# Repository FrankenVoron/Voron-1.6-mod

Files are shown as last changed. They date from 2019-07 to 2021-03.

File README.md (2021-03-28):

This modification has been transformed to the official Voron V1.8! https://github.com/VoronDesign/Voron-1/tree/Voron1.8

The files here are no longer maintained but will be kept for reference.

# Voron-1.6-mod (Depreciated)

It's the Voron V1.6, but better! Now with linear rails for XY and a fully enclosable design.

This github page is being updated and developed. Please note that all of these STLs are derived from the Voron Design V1.6 and V2.1 printers--any mods present in this folder are small changes to the existing Voron Design STLs to support changing the linear rods of V1.6 to linear MGN9H rails similar to how V2.1's gantry is.

This mod is fully unsupported by the Voron Design team, support and discussion will be in a separate Discord group, link to be populated in the future.

Default size is 300x300x340mm, reducing it down to 250mm saves only about $25. 340mm is due to lack of availability of 360mm linear steppers.

Total BOM cost is around $750-800, which sits it between the Hypercube ($550), BLV MGN Cube ($1000) and the Railcore II 300ZL ($1300). 

Advantages over the HEVO:
    
    -Cast aluminum bed (vs. PCB bed) -> much flatter, consistent bed surface
    -Linear rails for XY (vs. linear rods) -> less sag
    -AC heated bed (lower current to the bed, less load on the 24V power supply, quieter)
    -SKR 1.3 board with silent TMC2209 drivers vs. RAMPS board and loud A4988 drivers
    -Integrated Octoprint remote web control through Raspberry Pi
    -True 32 bit board with Klipper control
    -Mobius 3 extruder with Bondtech gears vs. Titan extruder (higher torque, grabs filament from both sides)
    -Enclosed build volume

Advantages over the Railcore:
    
    -Significantly cheaper
    -Easily enclosable
    -No risk of catching hands or tools on CoreXY belts

[V1.6 Mod BOM Link (In Process, NOT FINAL)](https://docs.google.com/spreadsheets/d/1ig14b1j8-F_122QWTeGj5dSmB8Jl30DImUAANSiHRPc/edit?usp=sharing)

[V1.6 Mod Fusion 360 Assembly (300^3)](https://a360.co/2MlttV1) <- will be updated to 300x300x340mm

V1.6 Mod

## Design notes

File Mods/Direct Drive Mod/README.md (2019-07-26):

# FT-V

Beta mod to add a BMG direct drive extruder on to the top of the carriage. Note--the VORON cable cover doors will not fit with this mod, and it may be difficult to find a place for the wires in your hotend. 

This is largely untested at the moment. Use at your own risk.

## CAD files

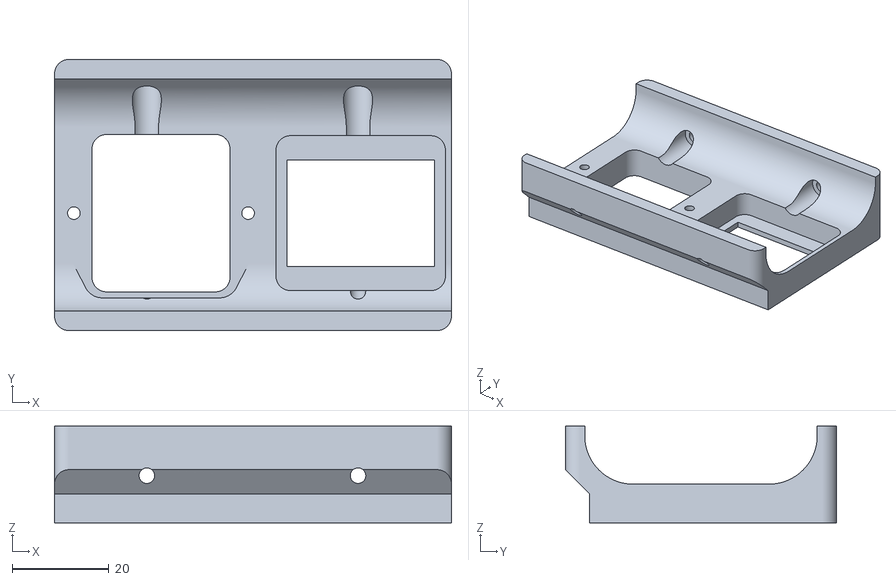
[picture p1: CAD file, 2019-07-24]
STLs/Bottom Skirts (Stock V1.6)/mains_plug_panel_filter_inlet+separate_breaker.STL
82.0 x 56.0 x 20.0

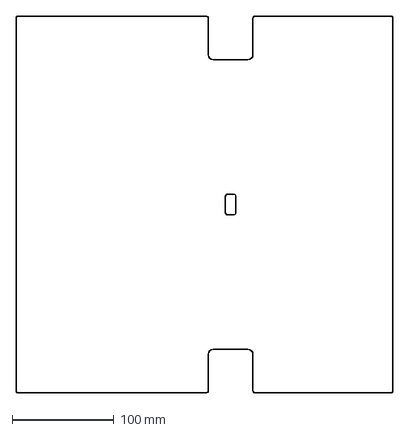
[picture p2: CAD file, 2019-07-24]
DXFs/Deck Panel - Stock^3.DXF
370.0 x 370.0 mm

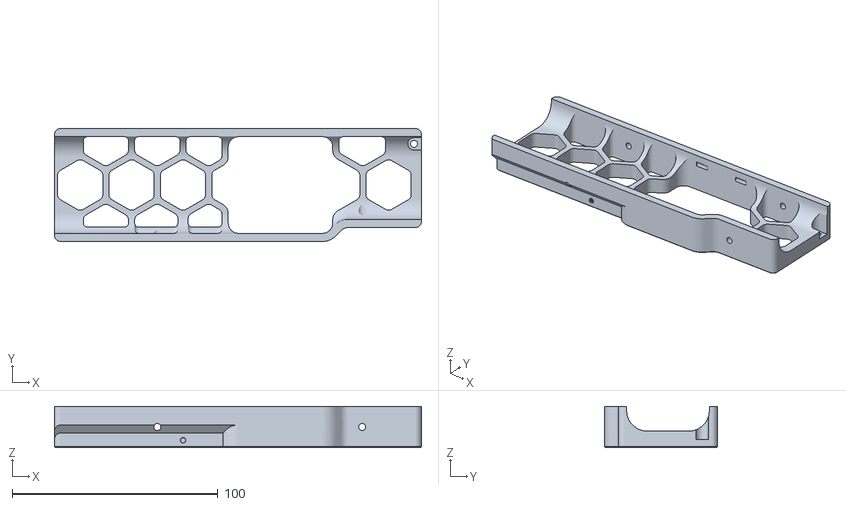
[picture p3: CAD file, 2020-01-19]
Mods/Bottom Skirts 300 Spec/front_rear_skirt_b_x2.stl
178.5 x 55.0 x 20.0

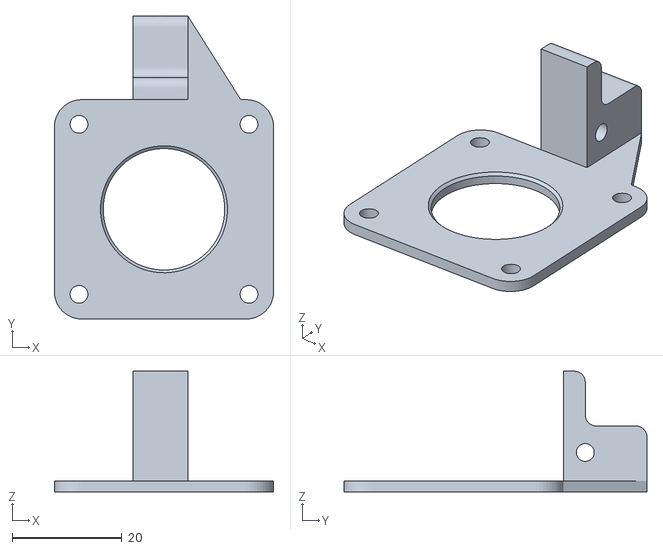
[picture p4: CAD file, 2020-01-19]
Mods/Direct Drive Mod/Direct_Drive_BMG_Mount.stl
40.0 x 55.3 x 22.0

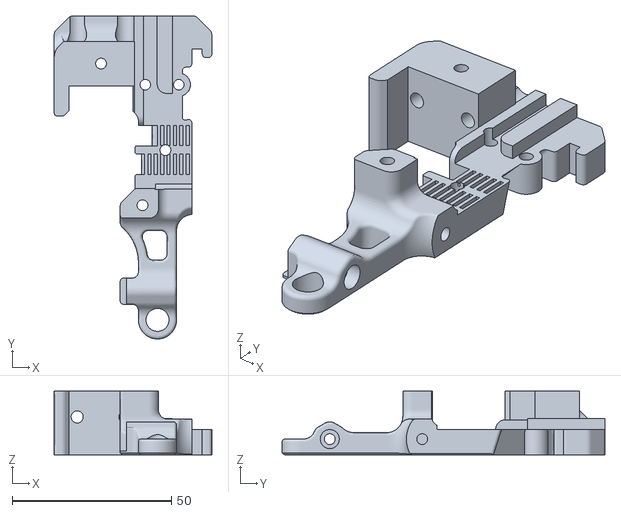
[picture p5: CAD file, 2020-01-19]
Mods/Omron X Carriage/x_carriage_frame_left_omron.stl
49.5 x 101.4 x 20.0

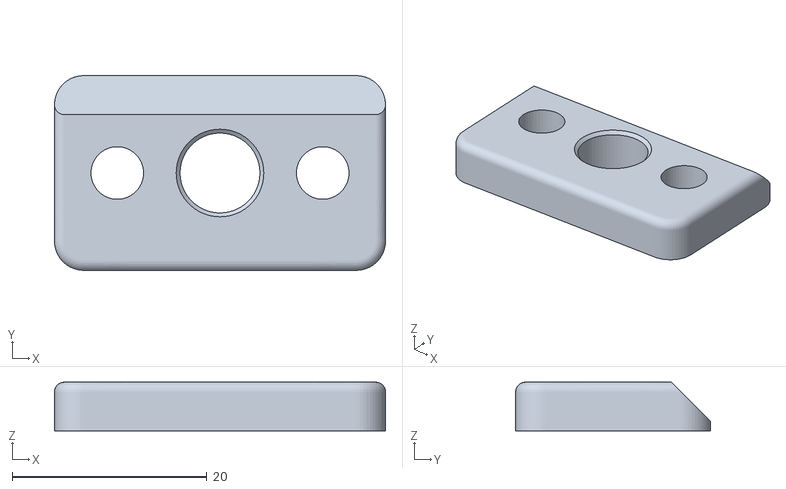
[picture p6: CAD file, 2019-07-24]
STLs/Bed (Stock V1.6)/z_shaft_retainer_x8.stl
34.0 x 20.0 x 5.00

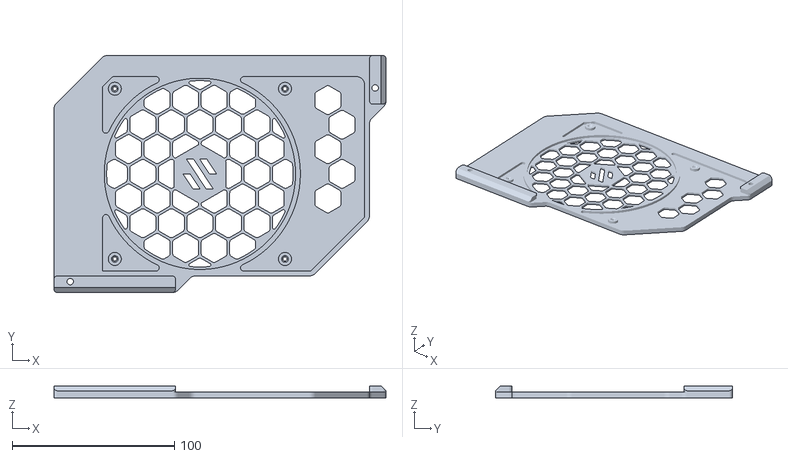
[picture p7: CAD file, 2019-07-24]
STLs/Bottom Skirts (Stock V1.6)/fan_mount.stl
204.8 x 146.2 x 7.70

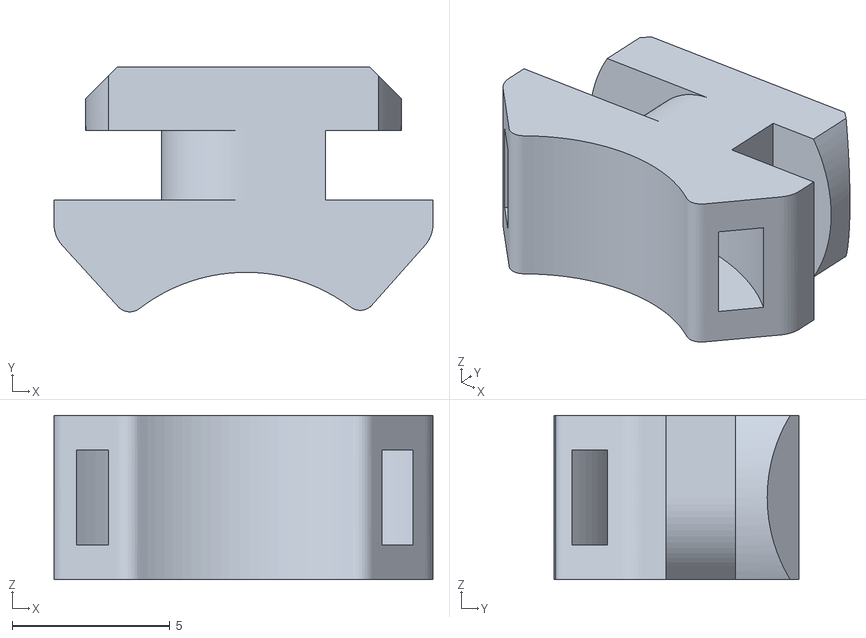
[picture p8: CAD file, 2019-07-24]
STLs/Cable Management (Stock V1.6)/wire_harness_anchor_x5.stl
12.0 x 7.75 x 5.20

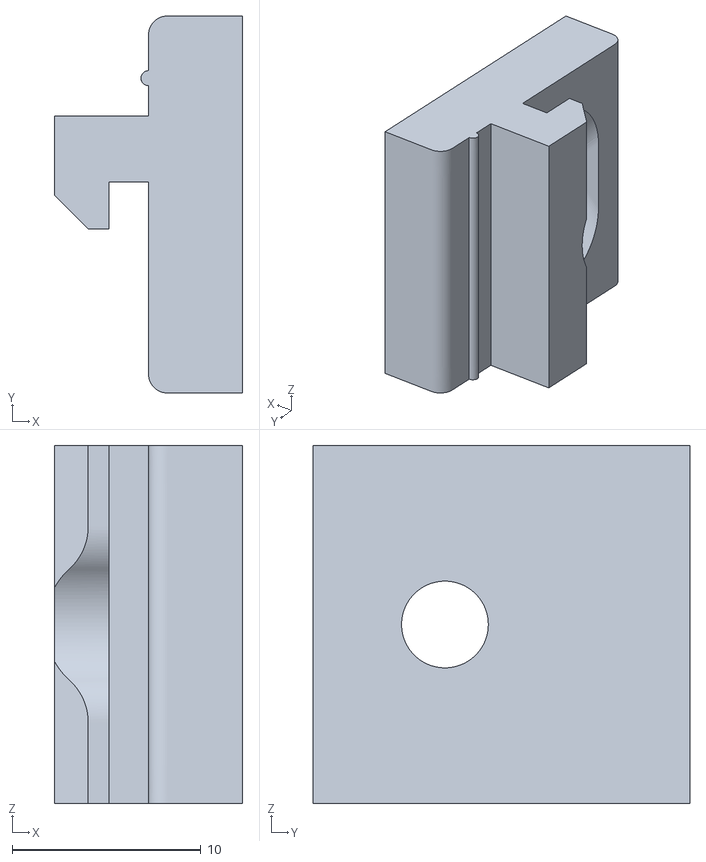
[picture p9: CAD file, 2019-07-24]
STLs/Electronics Brackets (Stock V1.6)/psu_mount_clip_x2.stl
10.0 x 20.0 x 19.0

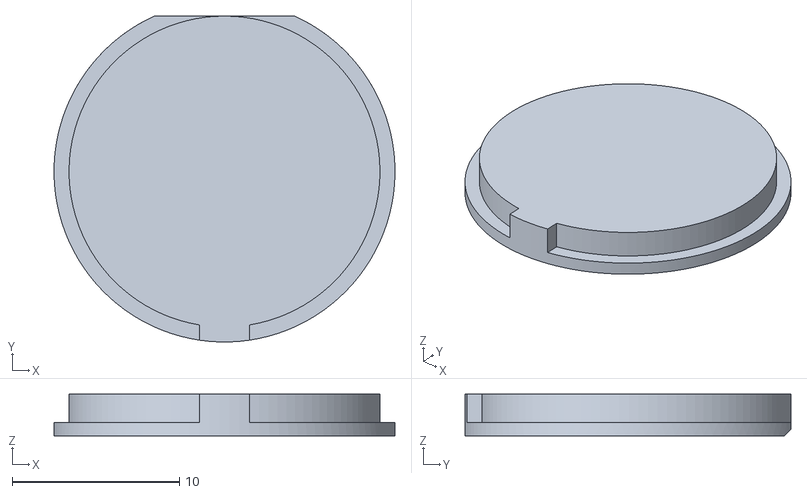
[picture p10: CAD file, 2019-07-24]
STLs/FSR Z Endstop (Stock V1.6)/fsr_strike_plate.stl
20.4 x 19.5 x 2.50

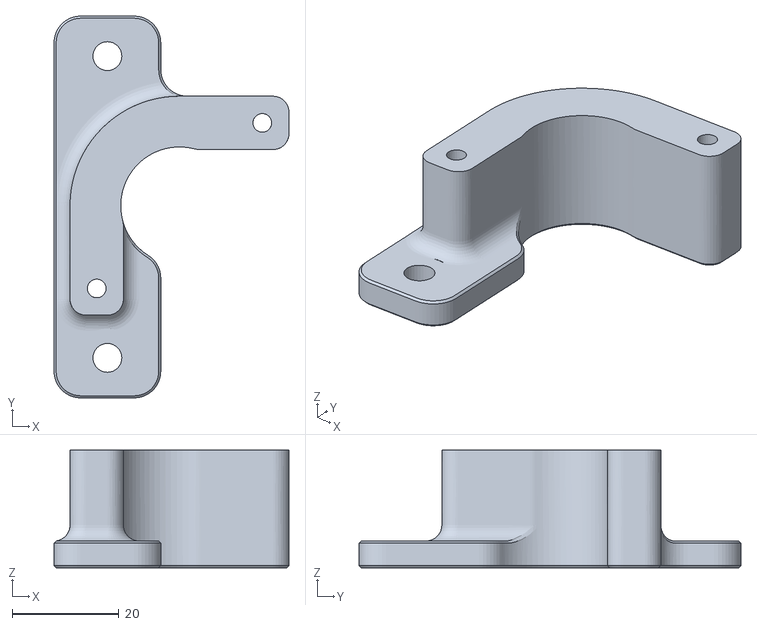
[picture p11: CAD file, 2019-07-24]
STLs/Gantry/AB Drives (V1.6 Mod)/a_motor_mount.stl
44.0 x 71.5 x 22.0

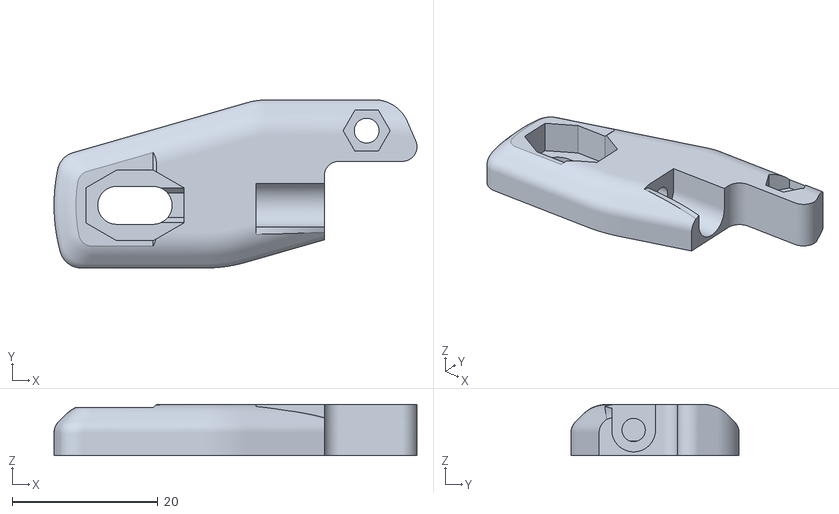
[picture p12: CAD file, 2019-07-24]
STLs/Gantry/Front Idlers (V2.1 Mod)/_front_tensioner_cap_lower_left.stl
49.8 x 23.1 x 7.00

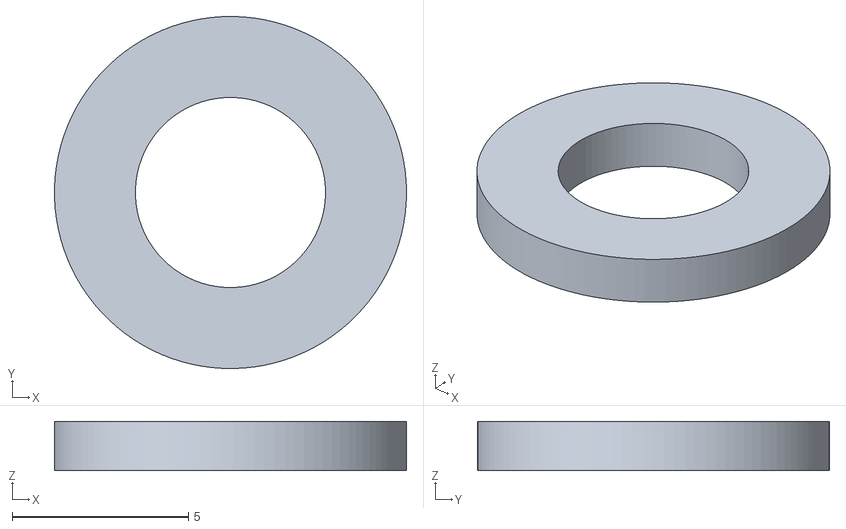
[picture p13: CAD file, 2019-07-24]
STLs/Gantry/small_bearing_spacer_x4.stl
10.00 x 10.00 x 1.40

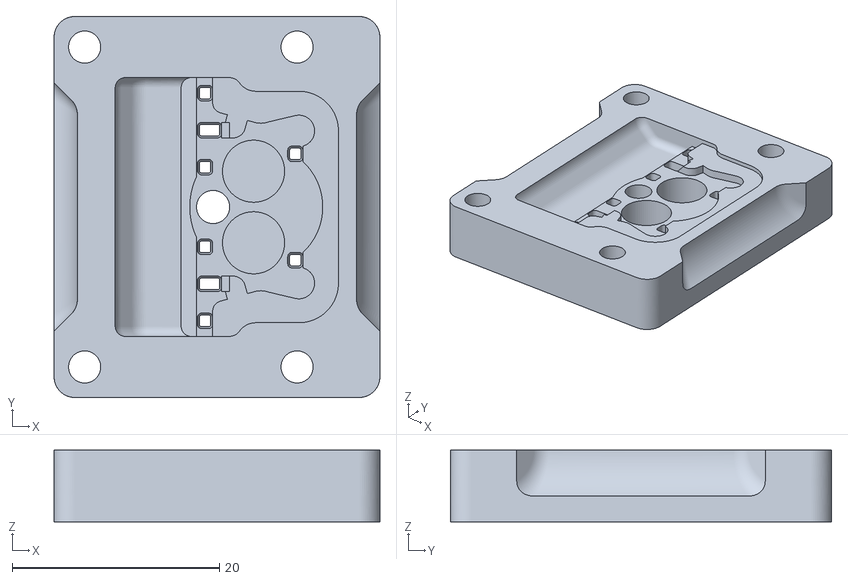
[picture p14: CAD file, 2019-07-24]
STLs/Gantry/X Carriage (V2.1 Mod)/Toolhead/Mosquito Hotend Sock/mosquito_sock_mold_top.stl
31.5 x 36.8 x 6.95

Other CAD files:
STLs/Gantry/X Carriage (V2.1 Mod)/Toolhead/v6_+_mosquito_cooling_fan_duct_left.STL
STLs/Gantry/X Carriage (V2.1 Mod)/x_carriage_frame_left.stl
STLs/Gantry/XY Joints (V2.1 Mod)/XY_Topbrace_Left_V1.6Mod.stl
STLs/LCD Module (Stock V1.6)/mount_base_b.stl
DXFs/Bottom Panel - Stock^3.DXF
Mods/Bottom Skirts 300 Spec/front_rear_skirt_a_x2.stl
Mods/Bottom Skirts 300 Spec/side_skirt_a_x2.stl
Mods/Bottom Skirts 300 Spec/side_skirt_b_x2.stl
Mods/Direct Drive Mod/X_Carriage_Frame_Left_Direct_MGN9.stl
Mods/Direct Drive Mod/X_Carriage_Frame_Right_Direct_MGN9.stl
Mods/Omron X Carriage/connector_cover_a_x1_Rev1.stl
Mods/Omron X Carriage/connector_cover_b_x1_Rev1.stl
Mods/Omron X Carriage/x_carriage_frame_right_omron.stl
Mods/Omron X Carriage/x_carriage_frame_zipchain_bar_x1_Rev1.stl
STLs/Bed (Stock V1.6)/leadscrew_block_x2.stl
STLs/Bed (Stock V1.6)/z_bearing_block_a_x2.stl
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

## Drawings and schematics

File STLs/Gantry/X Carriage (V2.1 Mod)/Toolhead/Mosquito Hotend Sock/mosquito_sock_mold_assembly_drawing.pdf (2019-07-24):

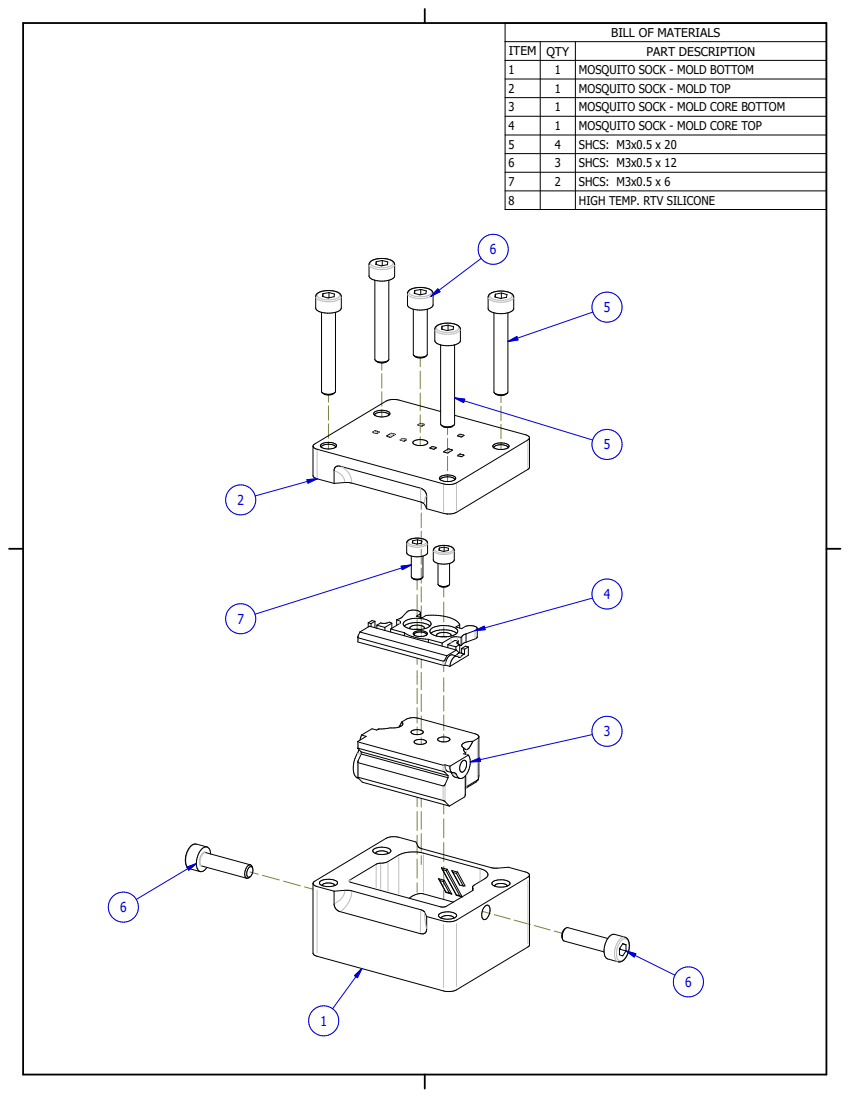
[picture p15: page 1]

BILL OF MATERIALS

ITEM | QTY | PART DESCRIPTION
1 | 1 | MOSQUITO SOCK - MOLD BOTTOM
2 | 1 | MOSQUITO SOCK - MOLD TOP
3 | 1 | MOSQUITO SOCK - MOLD CORE BOTTOM
4 | 1 | MOSQUITO SOCK - MOLD CORE TOP
5 | 4 | SHCS: M3x0.5 x 20
6 | 3 | SHCS: M3x0.5 x 12
7 | 2 | SHCS: M3x0.5 x 6
8 | | HIGH TEMP. RTV SILICONE

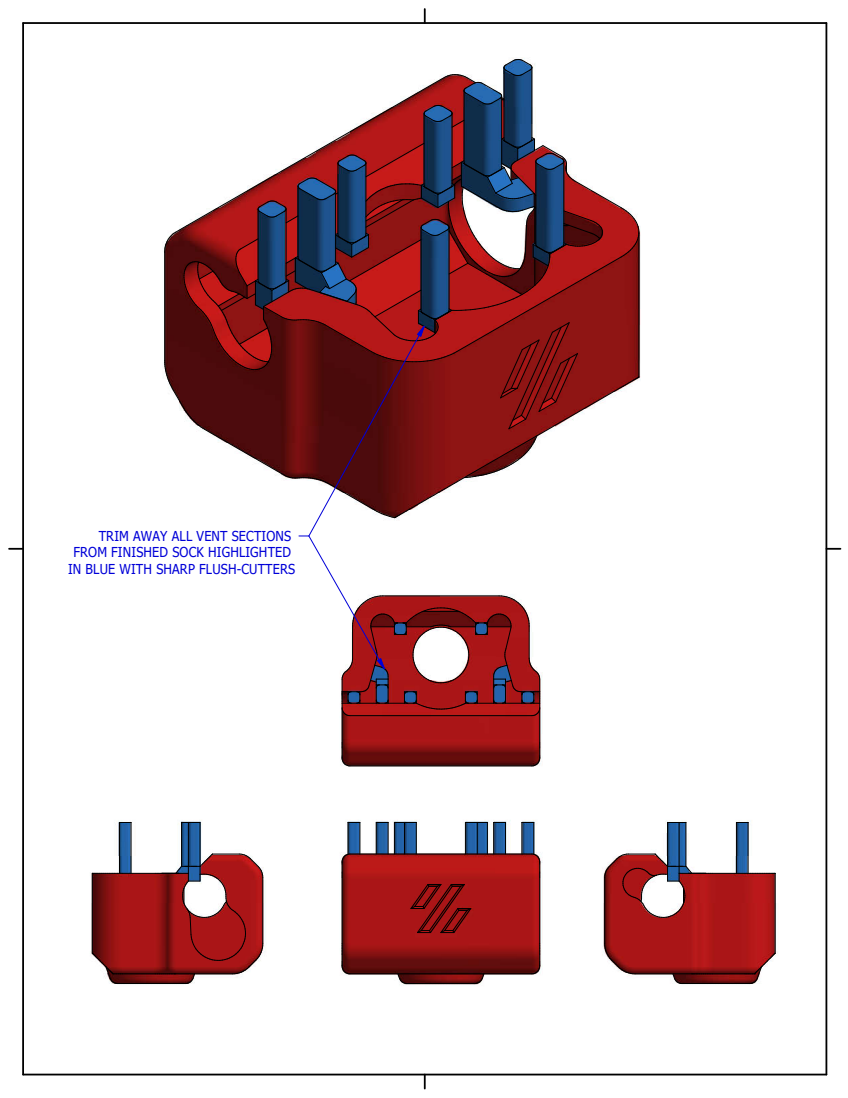
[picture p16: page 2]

TRIM AWAY ALL VENT SECTIONS
FROM FINISHED SOCK HIGHLIGHTED
IN BLUE WITH SHARP FLUSH-CUTTERS

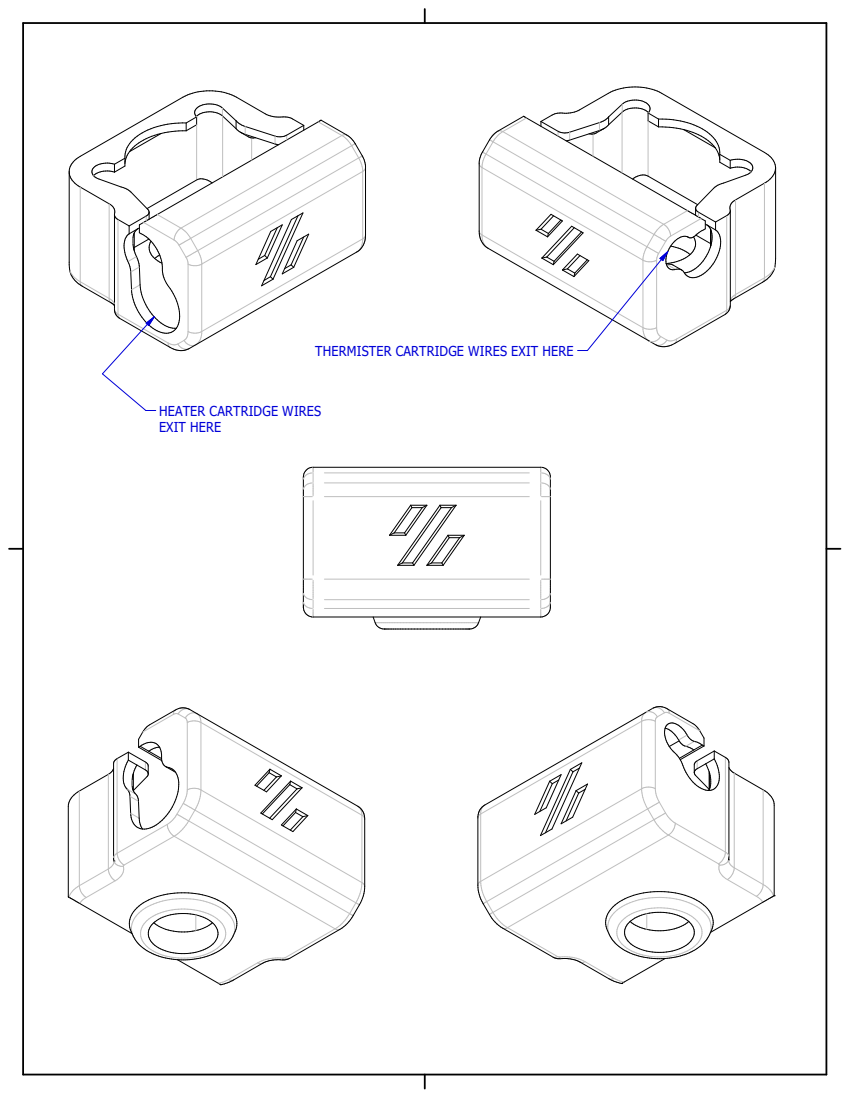
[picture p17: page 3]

THERMISTER CARTRIDGE WIRES EXIT HERE

HEATER CARTRIDGE WIRES
EXIT HERE

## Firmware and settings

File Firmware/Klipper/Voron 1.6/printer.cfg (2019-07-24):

# This file serves as documentation for config parameters of corexy
# style printers. One may copy and edit this file to configure a new
# corexy printer. Only parameters unique to corexy printers are
# described here - see the "example.cfg" file for description of
# common config parameters.

# DO NOT COPY THIS FILE WITHOUT CAREFULLY READING AND UPDATING IT
# FIRST. Incorrectly configured parameters may cause damage.

# Pinouts for RAMPS 1.4
# X_STEP_PIN         ar54
# X_DIR_PIN          ar55
# X_ENABLE_PIN       ar38
# X_MIN_PIN          ar3
# X_MAX_PIN          ar2
# Y_STEP_PIN         ar60
# Y_DIR_PIN          ar61
# Y_ENABLE_PIN       ar56
# Y_MIN_PIN          ar14
# Y_MAX_PIN          ar15
# Z_STEP_PIN         ar46
# Z_DIR_PIN          ar48
# Z_ENABLE_PIN       ar62
# Z_MIN_PIN          ar18
# Z_MAX_PIN          ar19
# E0_STEP_PIN        ar26
# E0_DIR_PIN         ar28
# E0_ENABLE_PIN      ar24
# E1_STEP_PIN        ar36
# E1_DIR_PIN         ar34
# E1_ENABLE_PIN      ar30
# SERVO_0_PIN        ar11
# SERVO_1_PIN        ar6
# SERVO_2_PIN        ar5
# SERVO_3_PIN        ar4
# D10		         ar10
# D9         		 ar9
# D8    		     ar8
# TEMP_0_PIN         analog13
# TEMP_1_PIN         analog14
# TEMP_2_PIN		 analog15

# The stepper_x section is used to describe the X axis as well as the
# stepper controlling the X+Y movement.
[stepper_x]
step_pin: ar54
dir_pin: ar55
enable_pin: !ar38
step_distance: 0.0125
endstop_pin: ^ar3
position_min: 0
position_endstop: 240
position_max: 240
homing_speed: 50
homing_positive_dir: true

# The stepper_y section is used to describe the Y axis as well as the
# stepper controlling the X-Y movement.
[stepper_y]
step_pin: ar60
dir_pin: ar61
enable_pin: !ar56
step_distance: 0.0125
endstop_pin: ^ar14
position_min: 0
position_endstop: 228
position_max: 228
homing_speed: 50
homing_positive_dir: true

[stepper_z]
step_pin: ar46
dir_pin: !ar48
enable_pin: !ar62
step_distance: .0025
endstop_pin: ^ar18
# FSR Nozzle Probe is optional on 1.6 and for when Klipper actually supports
# relative mesh bed. Currently it's only using Probe offset
endstop_pin: probe:z_virtual_endstop
position_max: 240
position_min: -5

[stepper_z1]
step_pin: ar26
dir_pin: !ar28
enable_pin: !ar24
step_distance: .0025

[homing_override]
set_position_z: 0
gcode:
    G1 Z5 F500
    G28 X0 Y0
    G0 X120 Y79 F5000
    G28 Z0
    G0 Z5 F500
axes: z

[extruder]
step_pin: ar36
dir_pin: ar34
enable_pin: !ar30
step_distance: 0.001725987
nozzle_diameter: 0.400
filament_diameter: 1.750
heater_pin: ar8
sensor_type: ATC Semitec 104GT-2
sensor_pin: analog13
max_extrude_only_distance: 200.0
control: pid
pid_Kp: 21.759
pid_Ki: 1.1
pid_Kd: 106.889
min_temp: 0
max_temp: 250

# thermally controlled hotend fan
[heater_fan hotend_fan]
pin: ar10
max_power: 1.0
kick_start_time: 0.100
heater: extruder
heater_temp: 50.0
fan_speed: 1.0

[heater_bed]
heater_pin: ar11
sensor_type: EPCOS 100K B57560G104F
sensor_pin: analog14
control: pid
pid_Kp=63.832
pid_Ki=3.404
pid_Kd=299.213
min_temp: 0
max_temp: 130

[fan]
pin: ar9

# extended G-Code command Z_TILT_ADJUST can be used to level gantry
[z_tilt]
# belt locations from orign 0,0
z_positions:
    -40,114
    272,114
# probing locations for gantry leveling
points:
    20,79
    114,79
    198,79
speed: 150
horizontal_move_z: 5

[bed_mesh]
speed: 150
samples: 2
horizontal_move_z: 4
min_point: 25,5
max_point: 203,153
probe_count: 3,3
; algorithm: bicubic

[mcu]
serial: /dev/ttyACM0
pin_map: arduino

[probe]
pin: ^ar19
y_offset: 35.0
# Tune this for Z offset
z_offset: 0.5
speed: 2.0

[printer]
kinematics: corexy
max_velocity: 300
max_accel: 2000
max_z_velocity: 25
max_z_accel: 30
square_corner_velocity: 5.0


[display]
lcd_type: st7920
cs_pin: ar16
sclk_pin: ar23
sid_pin: ar17
encoder_pins: ^!ar31, ^!ar33
click_pin: ^!ar35

# use G32 to level your bed
[gcode_macro g32]
gcode:
    Z_TILT_ADJUST
    Z_TILT_ADJUST
    G28
    G0 X115 Y115 Z10 F6000

#    Use print_start for you slicer starting script
[gcode_macro print_start]
gcode:
    G28
    G32
# Uncomment if you wish to use mesh bed leveling    
;    BED_MESH_CALIBRATE
    G0 X0 Y0 Z0.3 F9000
    G92 E0
    G1 E14 F600
    G1 X100 E20 F1000
    G92 E0

#    Use print_end for you slicer ending script
[gcode_macro print_end]
gcode:
    TURN_OFF_HEATERS
    M107
    G92 E0
    G91
    G1 Z1 E-8 F300
    G90
    G0 X115 Y230 F3000
    M84

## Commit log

2019-07-24 Initial commit
    Initial upload of V1.6mod stls
    Joshua Longenecker - jdlongenecker@gmail.com
    [A_Drive_Lower V1.6Mod.stl, A_Drive_Upper V1.6Mod.stl, B_Drive_Lower V1.6Mod.stl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]
2019-07-26 Add BMG Direct Drive Extruder Mod
    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
    [Direct_Drive_BMG_Mount.stl, X_Carriage_Frame_Left_Direct_MGN9.stl, X_Carriage_Frame_Right_Direct_MGN9.stl]
2019-07-27 Updated with BOM link
2019-07-30 Add Fusion360 Assembly for 300mm printer
    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
2019-12-28 Omron probe X carriage
    [connector_cover_a_x1_Rev1.stl, connector_cover_b_x1_Rev1.stl, x_carriage_frame_left_omron.stl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]
2020-01-01 Enlarge skirts for 300 bed printers
    [front_rear_skirt_a_x2.stl, front_rear_skirt_b_x2.stl, side_skirt_a_x2.stl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]
2020-01-19 Fixed BMG mounting plate
    [BMG Plate.stl]
2020-01-19 renamed and moved BMG Plate
    [BMG Plate.stl, Direct_Drive_BMG_Mount.stl]
